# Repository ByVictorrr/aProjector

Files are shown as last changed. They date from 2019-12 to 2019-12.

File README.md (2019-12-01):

# [aProjector](https://github.com/ByVictorrr/VanD/tree/master/aProjector) - autofocusing Projector 

* Allows you to move the projector an arbitrary distance and auto focuses the image produced 

* Supports most touch screen phones ..

This project is based on the laws of optics in physics and the thin lens equation and the magnification of the thin Lens:

Thin Lens

Magnification single

Coding and wiring done by [@VicDelaplaine](https://twitter.com/VicDelaplaine) || https://byvictorrr.github.io

Machining, CAD, and assembly done by [@dvnielwvng](https://twitter.com/dvnielwvng?lang=en) || https://danielwang.github.io

## aProjector 

video

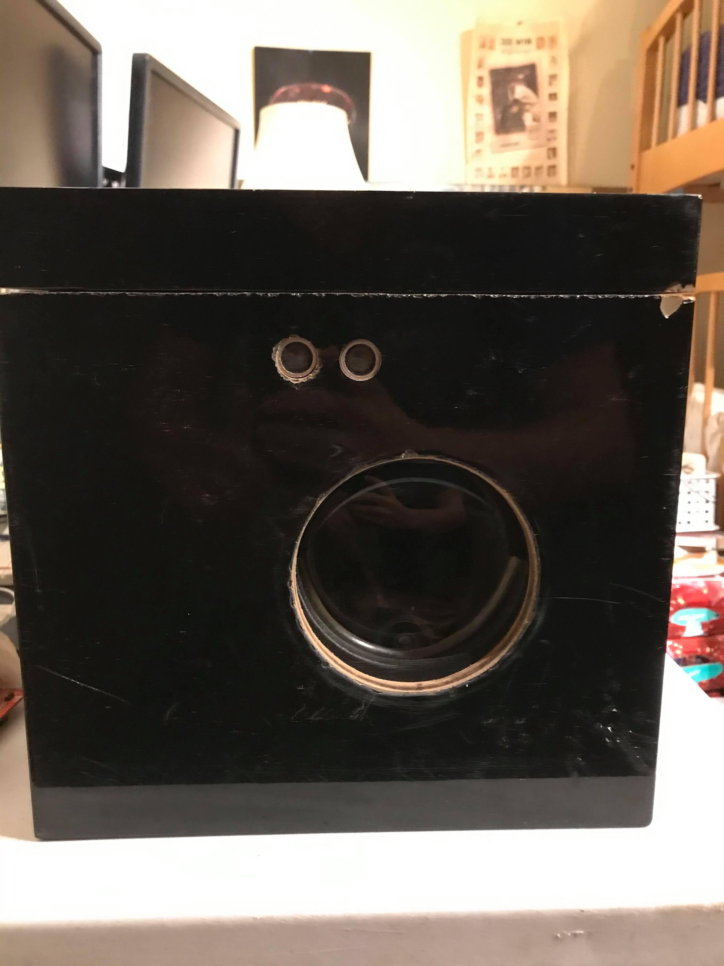
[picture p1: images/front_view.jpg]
front view


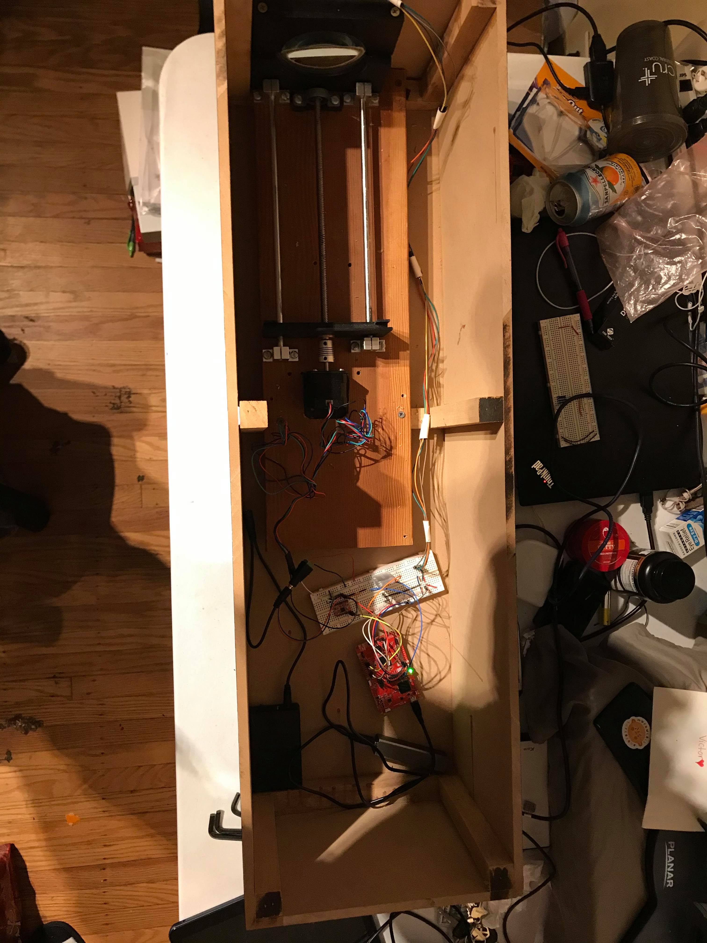
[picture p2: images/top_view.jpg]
top view


* Above shows the mechanism that we will use to put the phone in a fixed place
so we know the location on startup.

## What are lenses?

A lens is a transparent piece of glass or plastic with at least one curved surface. It gets its name from the Latin word for "lentil" (a type of pulse used in cooking), but don't let that confuse you. There's no real reason for this other than that the most common kind of lens (called a convex lens) looks very much like a lentil!

## How do lenses work?

A lens works by refraction: it bends light rays as they pass through it so they change direction. (You can read a full explanation of why this happens in our article on light.) That means the rays seem to come from a point that's closer or further away from where they actually originate—and that's what makes objects seen through a lens seem either bigger or smaller than they really are.

## Types of lenses

There are two main types of lenses, known as convex (or converging) and concave (or diverging).

### Converging lenses

In a convex lens (sometimes called a positive lens), the glass (or plastic) surfaces bulge outwards in the center giving the classic lentil-like shape. A convex lens is also called a converging lens because it makes parallel light rays passing through it bend inward and meet (converge) at a spot just beyond the lens known as the focal point.

imageOfConverging Lens

Convex lenses are used in things like telescopes and binoculars to bring distant light rays to a focus in your eyes.

### Diverging lenses

A concave lens is exactly the opposite with the outer surfaces curving inward, so it makes parallel light rays curve outward or diverge. That's why concave lenses are sometimes called diverging lenses. (One easy way to remember the difference between concave and convex lenses is to think of concave lenses caving inwards.)

imageOfDiverging Lens

Concave lenses are used in things like TV projectors to make light rays spread out into the distance. In a flashlight, it's easier to do this job with a mirror, which usually weighs much less than a lens and is cheaper to manufacture as well.

## Schematic:
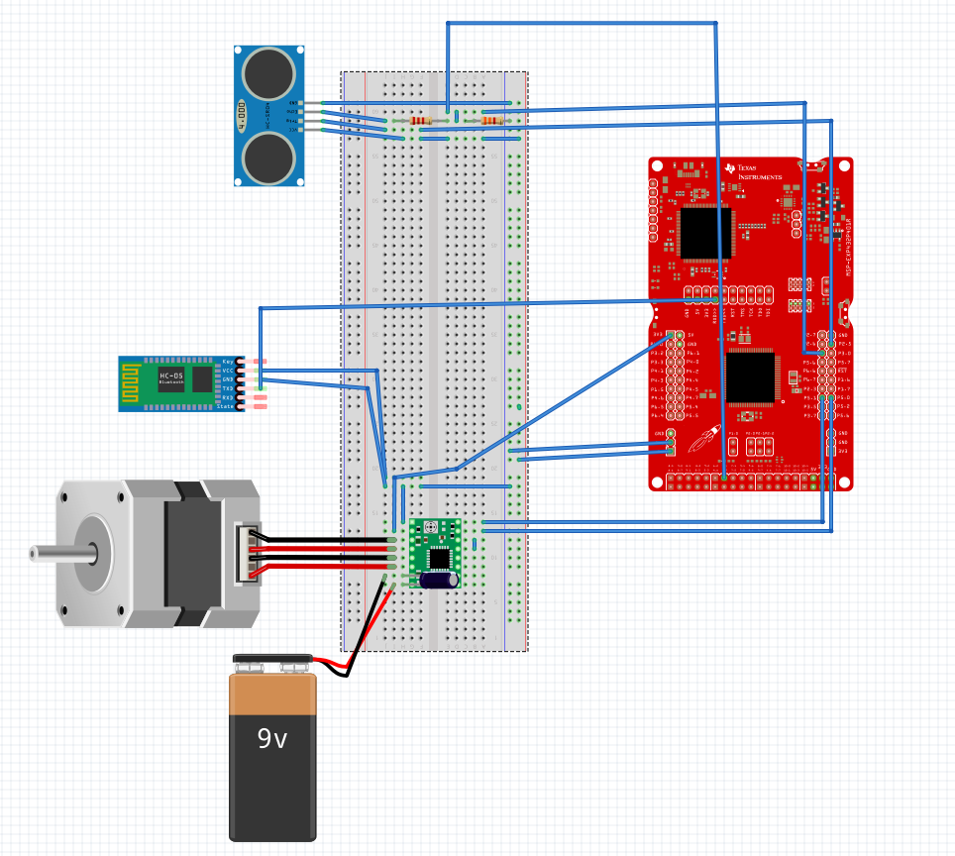
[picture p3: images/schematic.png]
schematic


## Hardware:

[MSP432p401R](https://www.amazon.com/Arduino-Pro-Mini-328-16MHz/dp/B004G53J5I)

[Phone](https://www.amazon.com/BLU-Advance-Unlocked-Smartphone-Black/dp/B072N6BD9V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)

The device that provides the image to be projected.

[Stepper motor](https://www.amazon.com/Longruner-Stepper-Uln2003-arduino-LK67/dp/B015RQ97W8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)

The stepper motor provides the force to translate the phone the optimal distance away from the lens 'd0' such that the image projected is clear. 'r' is the radius of the shaft of the stepper motor (2.5 mm).

[Ultra Sonic Sensor](https://www.amazon.com/Ultrasonic-Distance-Measuring-Compatible-Duemilanove/dp/B00SXZWMCS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<Paste>)

This sensor determines the distance between the front end of aProjector and the wall.

[12V Battery](https://www.amazon.com/Energizer-Alkaline-General-Purpose-Battery/dp/B00003IE4E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)
 
This is the power source for our system.
 
[HC-05(control)](https://www.amazon.com/)

After each use, this button serves as a reset such that 'd0' can be reset to the starting value.

[Converging Lens (20cm FL; 10cm diameter)](https://www.amazon.com/Eisco-Piece-Premium-Optical-Diameter/dp/B00BIKGMZ8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)

The lens amplifies the display on the phone.

## Mechanisms:

[Lead Screw Set](https://www.amazon.com/BIQU-Copper-Coupler-Bearing-Printer/dp/B01H1QGGEE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)

This lead screw set contains a lead screw, copper nut, coupler, and pillow bearings. The coupler will attach to the stepper motor and the lead screw, allowing the lead screw to rotate. Then, the nut will translate the rotation into a horizontal translation. The bearings provide support.

[Linear Shaft Rail Rod (x2)](https://www.amazon.com/dp/B07G14C2BB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)

The two rail rods will be on either side of the lead screw and will serve as a linear actuating track for the phone holder to travel on. 

## Other Equipment Needed:

[Dark Acrylic Plates](https://www.interstateplastics.com/Acrylic-Bronze-2370-Extruded-Paper-masked-transparent-11-Sheet-ACRZ0EFSH.php?sku=ACRZ0EFSH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)

These acrylic plates will serve as the walls that enclose the mechanisms and hardware.

Phone Holder

We 3D-printed a device to hold standard-sized smartphones such that their screens would be parallel to and facing the convex lens. The holder attaches to the nut and slides along the two rail rods.

Lens Holder

This 3D-printed device holds the lens in place, allowing the image from the phone screen to be projected accurately through it.

## Software:

aProjector's source code and schematic can be obtained in entirety from my Github: https://github.com/ByVictorrr/aProjector

## Resources
You can learn about lenses and refraction from a few places, including:

* [Derivation for Thin Lense EQN.](http://www.physics.louisville.edu/cldavis/phys299/notes/lo_lenses.html)

* [The Anatomy of a Lens](http://www.physicsclassroom.com/class/refrn/Lesson-5/The-Anatomy-of-a-Lens)

* [What is a lens](https://www.explainthatstuff.com/lenses.html)

## Contact
Point of Contact: [email](vdelaplainess@gmail.com)

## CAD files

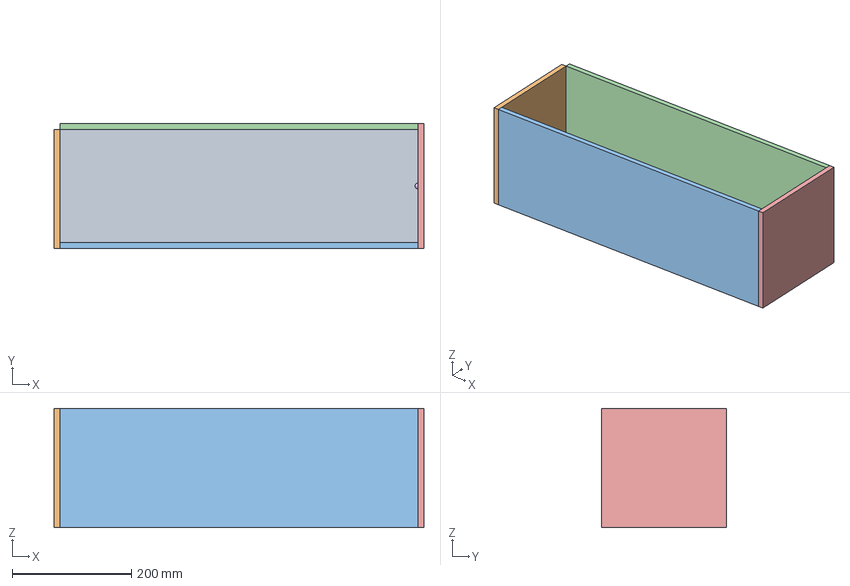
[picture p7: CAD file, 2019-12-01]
code_composer/final.FCStd
620.0 x 210.0 x 200.0 mm
Base
BackPlate
LeftSidePlate
RightSidePlate
FrontPlate

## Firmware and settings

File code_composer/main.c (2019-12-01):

#include "msp.h"
#include "Stepper.h"
#include "delay.h"
#include "UltraSonicSensor.h"
#include "bluetooth.h"
#include <math.h>

#define FOCAL_LENGTH 20.0 // cm
#define CIRCUMFERNCE .8 // 
#define RESET_DO 30.0 // cm
#define RESET_DI (FOCAL_LENGTH*RESET_DO)/(RESET_DO-FOCAL_LENGTH) //60cm

enum State {PREV, CURR};

float di[2]; // distance away from image

float _do(float di){
	float _do_var;
	if ((_do_var = (di *FOCAL_LENGTH)/(di-FOCAL_LENGTH)) <= 0)
		return 0;
	else
		return _do_var;
}
float get_revolutions(float *di){
	float diff = _do(di[CURR]) - _do(di[PREV]);
	return diff/CIRCUMFERNCE;
}



/*NOTE: Direction 
 * CCW - moves the phone back toward the motor
 * CW - moves the phone closer to the motor
 */
void main(void)
{
	float revolutions = 0;
	direction_t direction;
	init_UltraSonicSensor();
	init_Stepper(CW);
	init_BT();
	__enable_irq();

	di[PREV] = RESET_DI; // this is going to have to use the reset of do
	direction = CW;
	while(1){

		// STATE 1 - normal mode
	    if (bt == NORMAL_MODE){
			// step 1 - get di from get distance
 			di[CURR] = get_distance_cm_max();
			delay_us(1000);
			// step 2 - then use this to get revs  needed embeded is the direction
			revolutions = get_revolutions(di);
			delay_us(1000);
			direction = revolutions > 0 ? CCW : CW;
			// step 3 - then turn the motor needed	
			rotate(revolutions, direction);
			// step 4 - set prev = curr
			di[PREV] = di[CURR];
		// STATE 2 - reset do
		}else{
	        // restart to RESET_DI
			di[CURR] = RESET_DI;
			delay_us(1000);
			revolutions = get_revolutions(di);
			delay_us(1000);
			direction = revolutions > 0 ? CCW : CW;
			rotate(revolutions, direction);
			di[PREV] = di[CURR];
	    }
	    delay_us(10000);

	}
}

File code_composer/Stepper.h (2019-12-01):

/*
 * Stepper.h
 *
 *  Created on: Nov 16, 2019
 *      Author: victor
 */

#ifndef STEPPER_H_
#define STEPPER_H_

#define STEP BIT0
#define DIRECTION BIT1
#define STEP_PER_REV 200
#define CCW_PIN DIRECTION
#define CW_PIN ~DIRECTION
typedef enum{CCW, CW} direction_t;
// P5.0 - step
// P5.1 - DIRECTION
/**
 * main.c
 */
void init_Stepper(direction_t direction);
void step(int steps);
void set_direction(direction_t direction);
void rotate(float revolutions, direction_t direction);

#endif /* STEPPER_H_ */

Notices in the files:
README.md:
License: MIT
